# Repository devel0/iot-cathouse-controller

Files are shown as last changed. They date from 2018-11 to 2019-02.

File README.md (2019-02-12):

# iot-cathouse-controller

- [features](#features)
- [requirements](#requirements)
  * [thirdy part libraries](#thirdy-part-libraries)
- [initial setup](#initial-setup)
  * [set wifi ssid and pwd](#set-wifi-ssid-and-pwd)
  * [parameter configurations](#parameter-configurations)
  * [set temperature sensor ids](#set-temperature-sensor-ids)
- [config](#config)
  * [cooldown and system off](#cooldown-and-system-off)
  * [manual mode](#manual-mode)
  * [webapi](#webapi)
- [export csv data](#export-csv-data)
- [debug](#debug)
- [security considerations](#security-considerations)

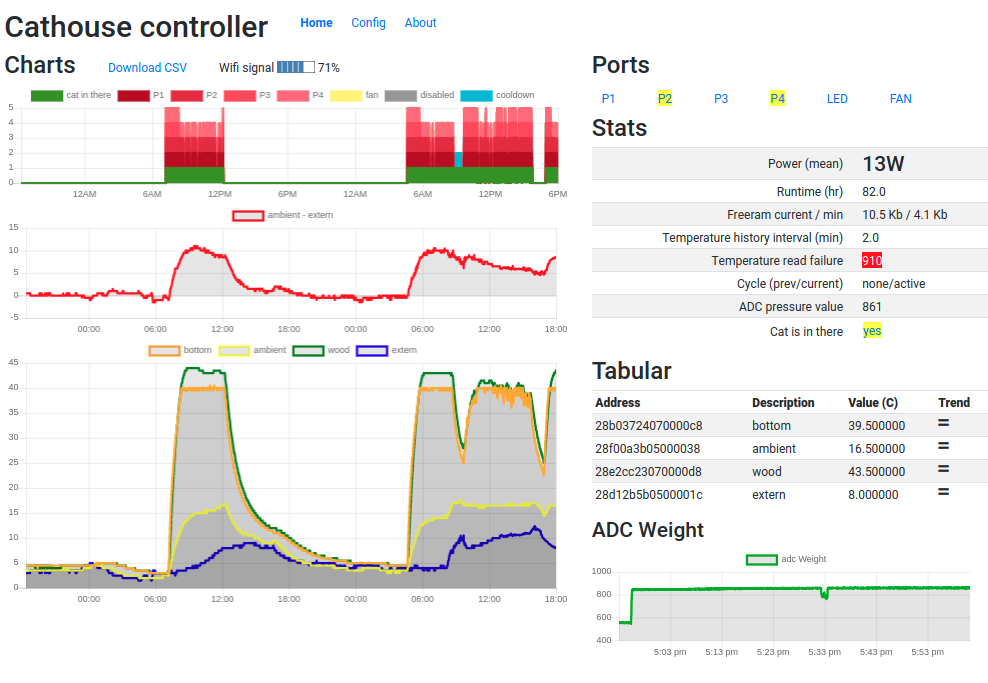
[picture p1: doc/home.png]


## features

- complete cathouse project ( building walls, heating system, weight detect, wifi control )
- wifi control automatic or manual through webapi ( [example](cathouse-analysis) )

## requirements

- hardware
  - [billing of materials](doc/bom.xlsx)
  - [instructables](https://www.instructables.com/id/DomoticCathouse/) to build and assembly cathouse parts
  - [nodemcu esp8266](https://www.google.com/search?q=nodemcu+esp8266)
  - [global schematics](https://easyeda.com/editor#id=|c888d1d962eb41688482b3634ec3ae96)
    - [mosfet driver](https://easyeda.com/editor#id=|8c9be83bc0324be699e9c5582d8d355a|41530c0b5fc0479b98395b739bd6d0e3)
    - [loadcell opamp](https://easyeda.com/editor#id=|20ec83ae7a4a4b50ac9ebe939533f176|184084caaad548a8a8d9fdd1c97d6a88|f6c7edf3d70e4a249dd6ca145c1bad17) and [sim](http://everycircuit.com/circuit/4874105232031744)
- software
  - [vscode arduino](https://github.com/devel0/knowledge/blob/master/electronics/vscode-arduino.md)
  - [esp8266 board plugin](https://github.com/esp8266/Arduino#installing-with-boards-manager)

### thirdy part libraries

- [ArduinoJsonWriter](https://github.com/maxpowel/ArduinoJsonWriter)
- [JsonStreamingParser](https://github.com/squix78/json-streaming-parser)
- [StringStream](https://gist.github.com/arcao/3252bb6e5e52493f03726ec32e61395c)

## initial setup

### set wifi ssid and pwd

connect to serial interface of esp8266 through usb cable with minicom at 115200 8N1 and issue `ctrl+c` to stop unsuccesful initial wifi connection then press `?` for SerialOS commands
- `set wifi ssid <ssid>` to set your own wifi ssid
- `set wifi pwd <pwd>` to set your own wifi pwd
- data save automatically into eeprom
- `reconnect` to test new wifi parameters
- check in the serial log which ip assigned to your device ( a better approach is to reserve a fixed wellknown ip address in your network by mapping it from the interface mac address also printed in serial log )

### parameter configurations

- connect to `http://cathouseip` and go to Config page

### set temperature sensor ids

in order to allow the system recognition of temperature sensor for bottom, wood, ambient and extern first there is the need to write down their ids ; use one of existing inet [articles](https://www.google.com/search?q=arduino+ds18b20+id) to find out.
write correspondent temperature IDs in fields ( 16 hex char foreach device )

### config

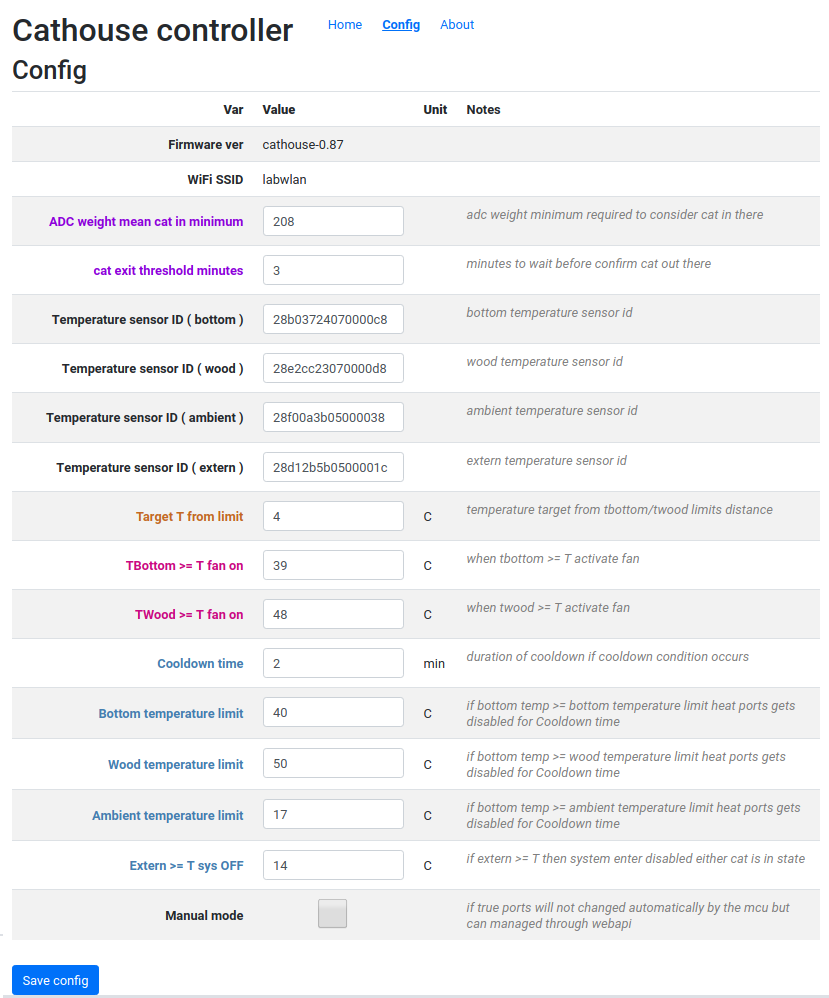
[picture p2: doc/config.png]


## heat modes

### auto mode

- when cat enters all ports enabled until reaches **Target T from limit** value from either one of bottom toward **Bottom temperature limit** or wood toward **Wood temperature limit**
- if some limit condition occurs system goes off for given cooldown time
  - bottom temp great or equals bottom temp limit
  - wood temp great or equals wood temp limit
  - ambient temp great or equals ambient temp limit
- if external temp great or equals 'Extern >= T sys OFF' then system goes off independently cat is in there or not
- ports are selected in order of preference as from [Config.h](cathouse-controller/Config.h) PORT_PREF
- trend delta can be configured in [Config.h](cathouse-controller/Config.h) TBOTTOM_TREND_DELTA_C

### manual mode

- in manual mode ports and fan can be controlled manually from web interface or webapi
- limit conditions still apply automatically entering the system in cooldown or disabled cycle mode
- led port can be toggled manually either in auto mode

### webapi

| **address** | **content-type** | **result example** |
|---|---|---|
| `/tempdevices` | json | `{"tempdevices":["28b03724070000c8","28f00a3b05000038","28e2cc23070000d8","28d12b5b0500001c"]}` |
| `/temp/devid` | text | retrieve temperature C of given `devid` device |
| `/info` | json | `{"wifiSignalStrength":-59, "statIntervalSec":2, "freeram":11464, "freeram_min":4168, "history_size":1455, "history_interval_sec":118, "temperatureHistoryFillCnt":1455, "temperatureHistoryOff":806, "temp_read_failure":915, "manualMode":false, "adcWeightArraySize":2048, "adcWeightArrayOff":273, "adcWeightArrayFillCnt":2048, "adcWeightArray":[848,847,849,848,...,850], "catIsInThere":true, "p1": false, "p2": true, "p3": false, "p4": true, "led": false, "fan": false, "temp_history_interval_min": 1.966667, "prev_cycle": "none", "current_cycle": "active", "runtime_hr": 82.190266, "Wh": 1087.330255}` |
| `/temphistory` | json | `[{"28b03724070000c8":[8.00,9.00]},{"28f00a3b05000038":[4.44,4]}]` |
| `/bithistories` | json | `{"catInThereHistory":[0,1,1],"p1History":[0,1,1],"p2History":[0,0,0],"p3History":[0,0,0],"p4History":[0,1,1],"fanHistory":[0,0,0],"disabledHistory":[0,0,0],"cooldownHistory":[0,0,0]}` |
| `/port/get/X` | text | `0` |
| `/port/set/X/{0,1}` | text | `OK` or `DENIED` if manualMode false |
| `/port/toggle/X` | text | `OK` or `DENIED` if manualMode false |
| `/setcatinthere/{0,1}` | text | `OK` |
| `/getconfig` | json | `{"tbottomLimit":45.00,"twoodLimit":60.00,"tambientLimit":17.00,"cooldownTimeMs":120000,"texternGTESysOff":14.00,"adcWeightMeanCatInMinimum":600,"catExitThresholdMin":3,"manualMode":false,"tbottomGTEFanOn":42.00,"twoodGTEFanOn":57.00,"targetTempFromLimit":4.00,"firmwareVersion":"cathouse-0.87","wifiSSID":"labwlan","tbottomId":"28b03724070000c8","twoodId":"28e2cc23070000d8","tambientId":"28f00a3b05000038","texternId":"28d12b5b0500001c"}` |
| `/saveconfig` | json POST | |

notes
- `temphistory`, `adcWeightArray`, `bithistories` are a set of measure where latest sample if the current one and previous are distant between each one from specified `history_interval_sec`
- valid ports in `/port/get` and `/port/set` are
  - heating ports ( 1, 2, 3, 4 )
  - led port ( 5 )
  - fan port ( 6 )

## export csv data

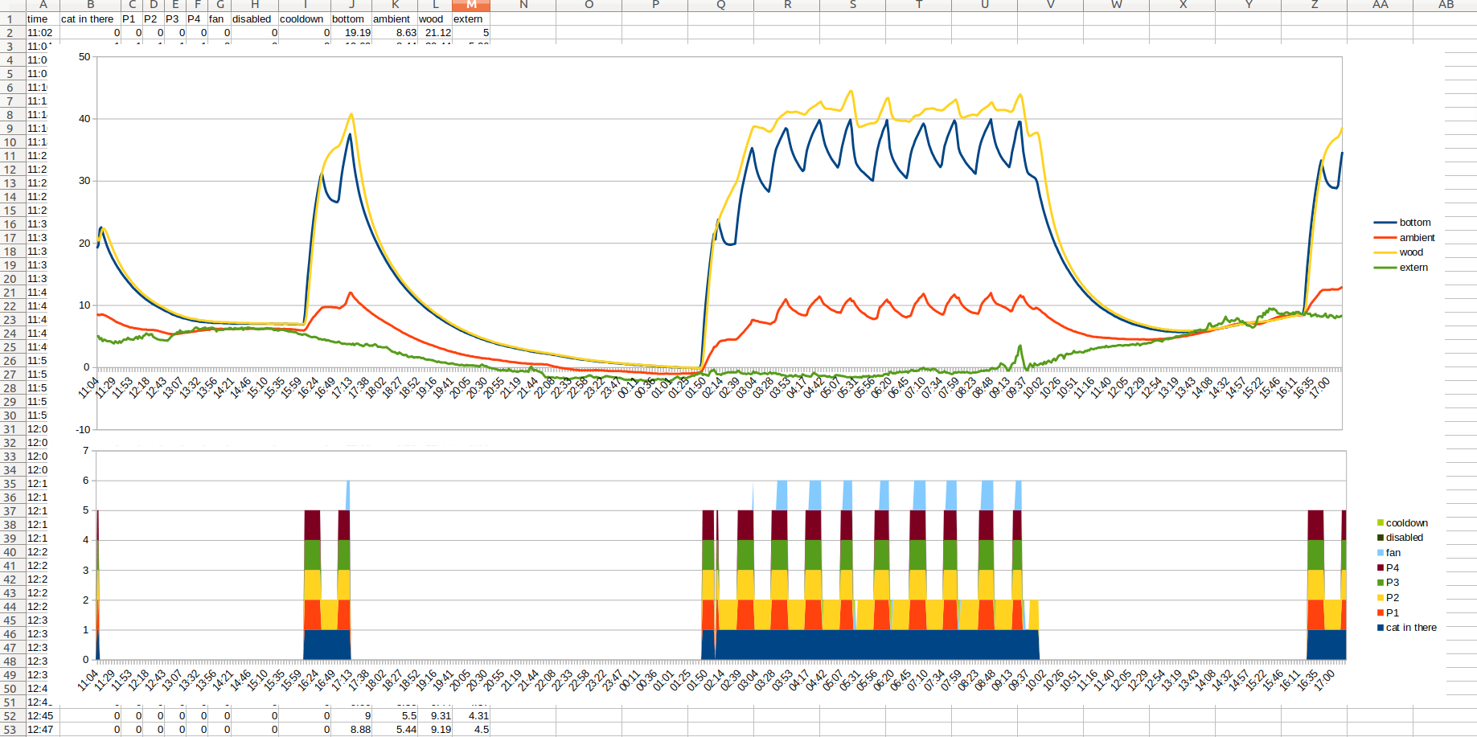
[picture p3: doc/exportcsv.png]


- data will be exported using decimal separator dot or comma accordingly to browser locale

## debug

```
cd cathouse-controller
code .
```

- to build or check compilation `CTRL+SHIFT+R`
- to upload through USB-serial `CTRL+SHIFT+U`

- when ENABLE_CORS enabled client side can be debugged without need to upload firmware again simply dragging `index.htm` to the browser so that `app.js` will loaded from local disk

## security considerations

- in release mode set [**ENABLE_CORS**](https://github.com/devel0/iot-cathouse-controller/blob/dbb4c67158c6660667ba5c55b46a064916e80611/cathouse-controller/Config.h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) to 0 to avoid browser requests from non owner html page
- on a internet facing page there is the need of a nginx proxy using a letsencrypt **https** certificate to ensure traffic flows in an encrypted channel ; plus there is the need to enable a page **basic authentication** ; see [here](https://github.com/devel0/knowledge/blob/cc771417542ff2cd5af335eec530da644a98c15a/webdevel/nginx-webapi-conf.md) for details

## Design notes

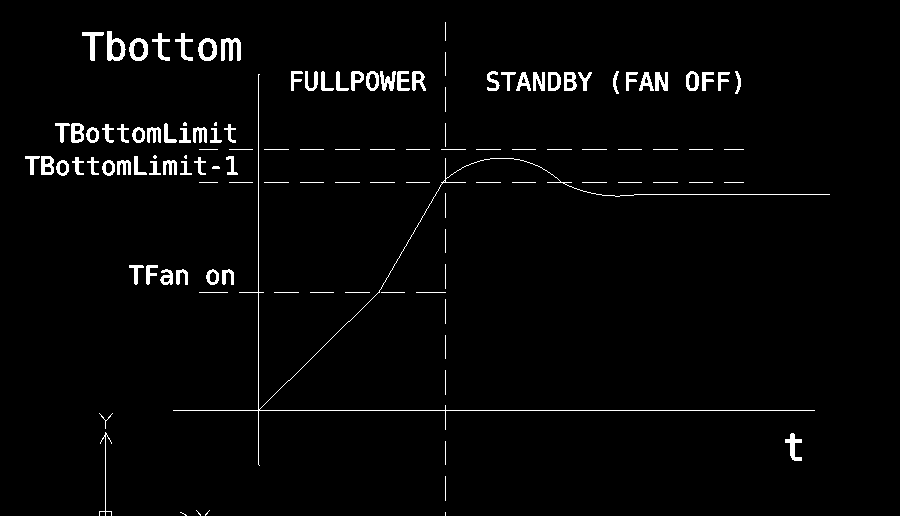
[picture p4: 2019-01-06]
doc/cycles.png

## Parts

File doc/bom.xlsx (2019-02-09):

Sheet: MATERIALS
qt | mu | description | L1 (mm) | L2 (mm) | thk (mm) | notes
2 |  | glass | 500 | 125 | 3
7 |  | polystyrene | 1000 | 500 | 10 | 4 x 830 x 600 + 2 x 556 x 600
13 |  | poplar plywood | 830 | 600 | 5 | 8 x 830 x 600 + 4 x 556 x 600 + 1 x 790 x 560
1 |  | poplar plywood | 830 | 400 | 5 | 1 x 700 x 400
4 |  | fir strip | 1000 | 97 | 10 | 2 x 780 + 2 x 550
1 |  | tierod M4 | 1000
2 |  | alu profile square hollow | 10 | 10 | 1000
2 |  | adhesive cold sealant | 25 | 5 | 4500
64 |  | screw | 15
12 |  | screw | 50
76 |  | washer | 10
2 | kg | refractory mortar

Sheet: 3DPRINT
part | qt | notes | license
spacer1.stl | 20 | top,bottom,front,back | MIT
spacer2.stl | 12 | left/right sides | MIT
spacer3.stl | 2 | door tierod holder | MIT
spacer4.stl | 2 | door fixating with tierod holder | MIT
cable-management.stl | 4 | ambient temp sensor and led wire holder | MIT
mosfet-driver-box | 1 |  | MIT
esp8266 holder | 1 | https://www.thingiverse.com/thing:3010027 | MIT
load-cell-5kg-contact-pad | 1 |  | MIT
load-cell-5kg-holder | 1 |  | MIT

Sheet: ELECTRONICS
category | qt | mu | description | code
fan | 1 |  | FAN 80mm 20mA @5V | Noctua NF-R8 Redux 1200
fan | 1 |  | resistor 3.3k ohm (5%)
heating | 1 |  | power transformer 24V 150W | MeanWell LRS-150-24
heating | 2 | m | Kanthal A1 AWG34 wire
heating | 4 |  | IRF740PBF mosfet
heating | 4 |  | TO-220 heatsink
heating | 4 |  | EL817 optocoupler
heating | 4 |  | PCB connector 1x2
heating | 4 |  | resistor 330 ohm (5%)
heating | 4 |  | resistor 10k ohm (5%)
led | 1 |  | white led flat 5mm 20mA
led | 1 |  | 2N2222 (1A max)
led | 1 |  | resistor 470 ohm (5%)
led | 1 |  | resistor 180 ohm (5%)
MCU | 1 |  | esp8266 nodemcu v3
power | 1 |  | power adaptor 5V 2A
temp sensor | 4 |  | ds18B20
temp sensor | 1 |  | resistor 4.7k ohm (1%)
weight sensor | 4 |  | loadcell 50kg SEN 10245
weight sensor | 1 |  | LM324N
weight sensor | 1 |  | PCB connector 1x2
weight sensor | 6 |  | resistor 39k (1%)
weight sensor | 1 |  | resistor 390 (5%)

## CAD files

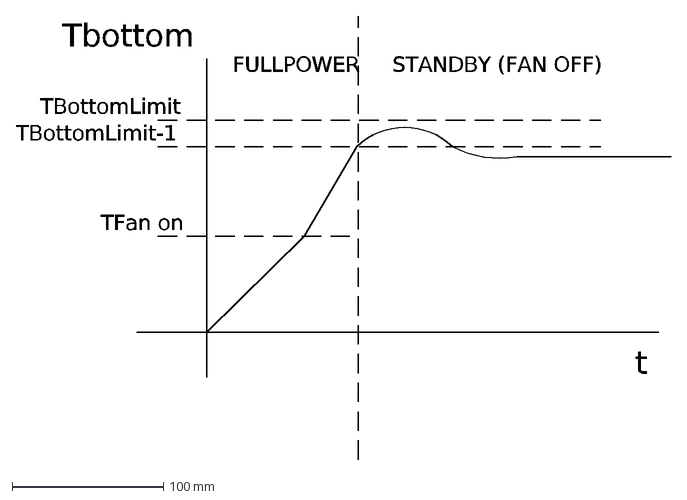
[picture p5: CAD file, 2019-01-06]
doc/auto-cycle.dxf
Tbottom
t
TFan on
TBottomLimit-1
TBottomLimit
FULLPOWER
STANDBY (FAN OFF)

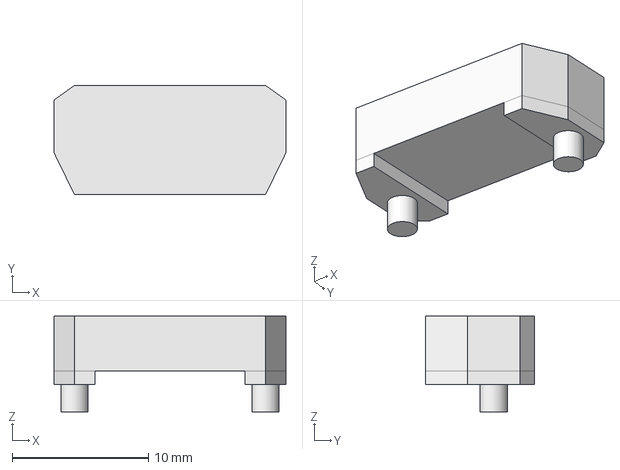
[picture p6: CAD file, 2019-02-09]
doc/cathouse-drawings/load-cell-5kg-contact-pad.fcstd
17.0 x 8.00 x 7.00 mm

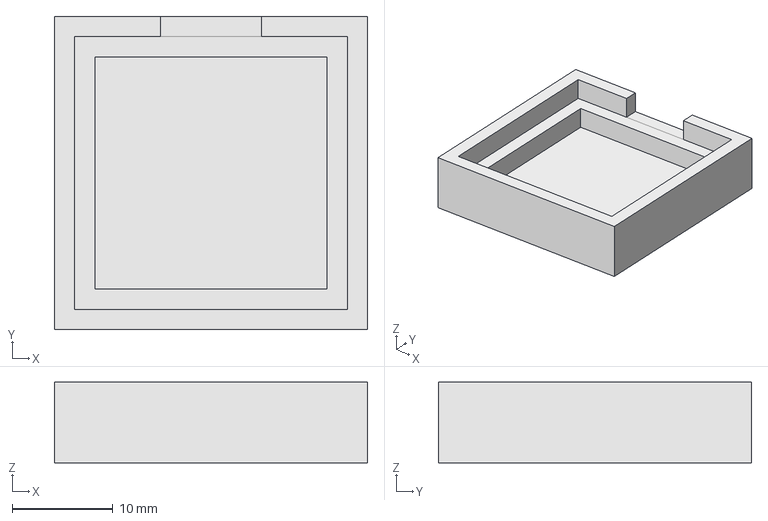
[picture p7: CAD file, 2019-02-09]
doc/cathouse-drawings/load-cell-5kg-holder.fcstd
31.0 x 31.0 x 8.00 mm

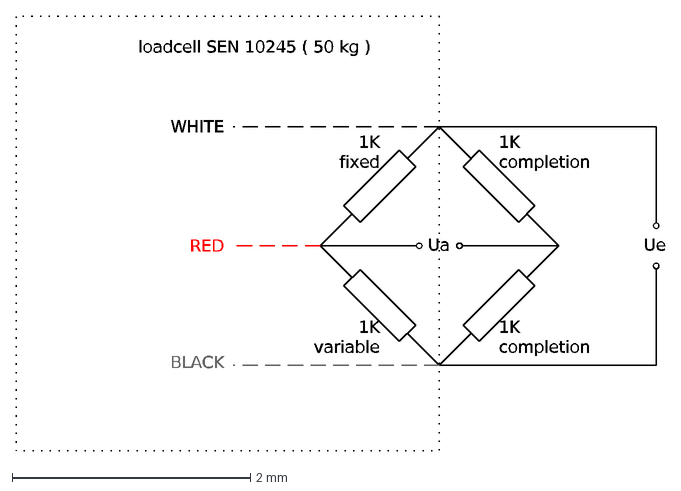
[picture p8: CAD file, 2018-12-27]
doc/loadcell-half-bridge-completion.dxf
1K completion
1K fixed
1K variable
Ua
Ue
RED
WHITE
BLACK
loadcell SEN 10245 ( 50 kg )

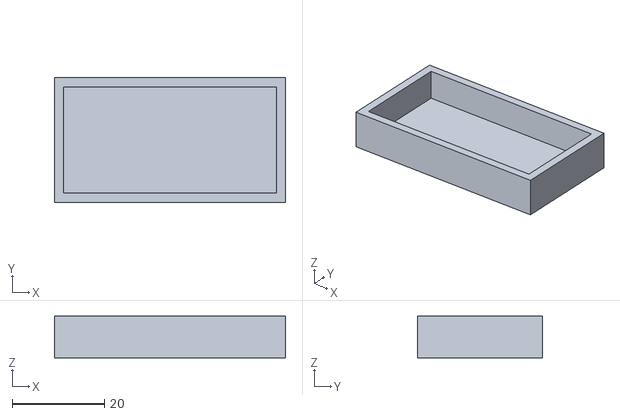
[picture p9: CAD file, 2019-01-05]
doc/cathouse-drawings/step-up-box.stl
50.0 x 27.0 x 9.00

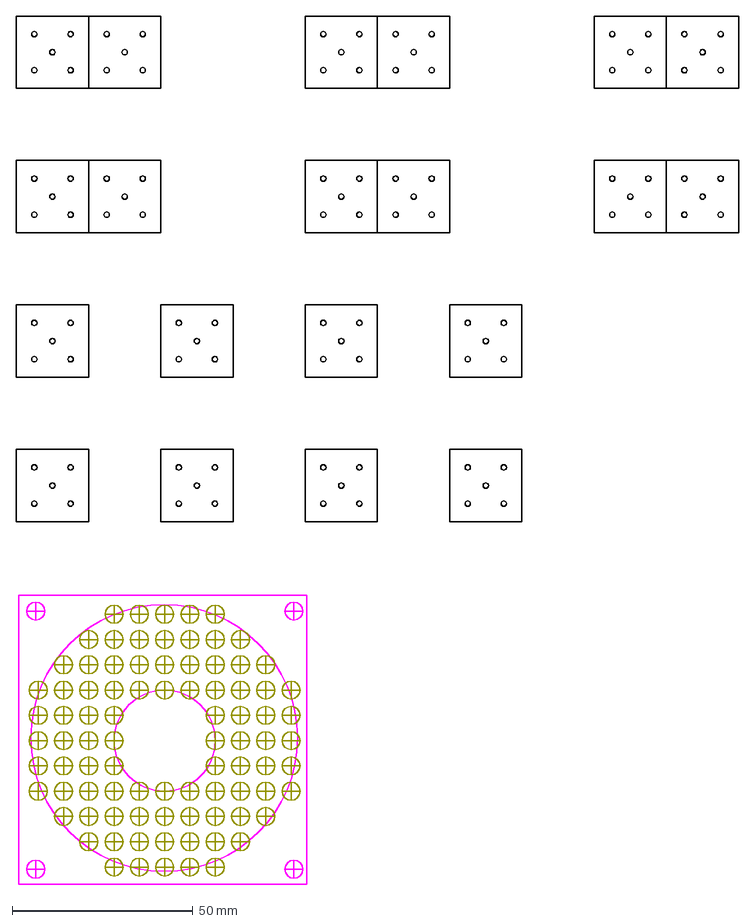
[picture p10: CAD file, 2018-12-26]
doc/cathouse-drawings/guidemask.dxf
200.0 x 240.3 mm

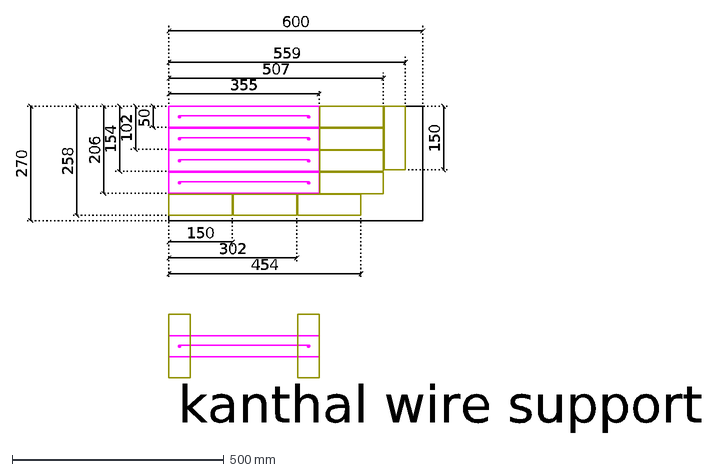
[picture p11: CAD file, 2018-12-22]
doc/cathouse-drawings/kanthal-wire-support.dxf
600
270
355
507
559
50
102
154
206
258
150
302
454
kanthal wire support

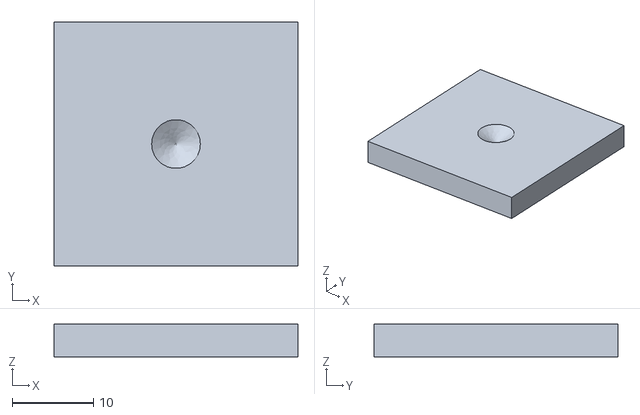
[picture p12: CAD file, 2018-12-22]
doc/cathouse-drawings/load-cell-top.stl
30.0 x 30.0 x 4.00

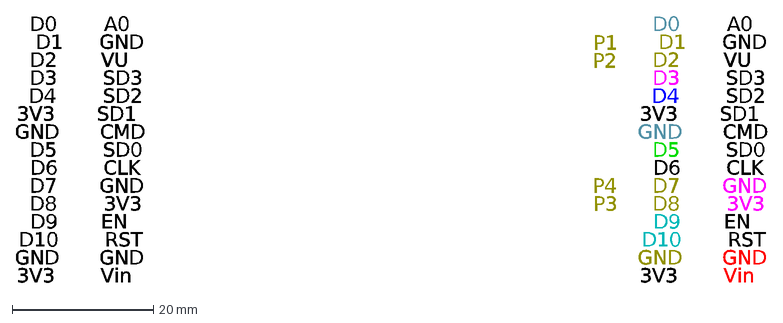
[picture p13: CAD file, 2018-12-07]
doc/cathouse-drawings/esp8266-labels.dxf
Vin
GND
RST
EN
3V3
CLK
SD0
CMD
SD1
SD2
SD3
VU
A0
D10
D9
D8
D7
D6
D5
D4
D3
D2
D1
D0
P1
P2
P4
P3

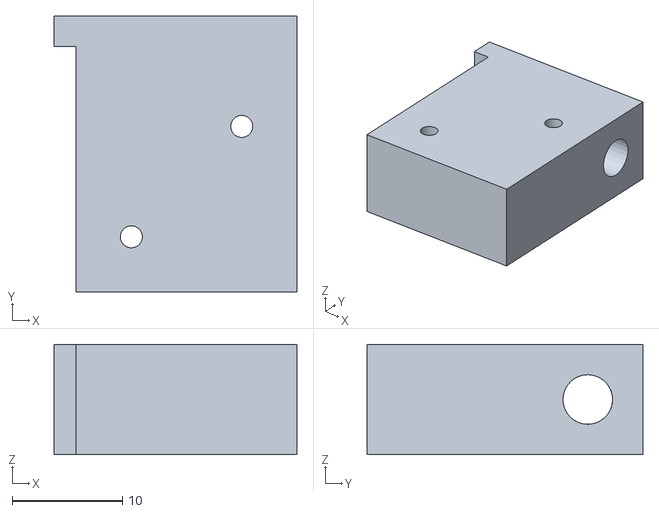
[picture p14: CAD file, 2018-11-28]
doc/cathouse-drawings/spacer4.stl
22.0 x 25.0 x 10.0

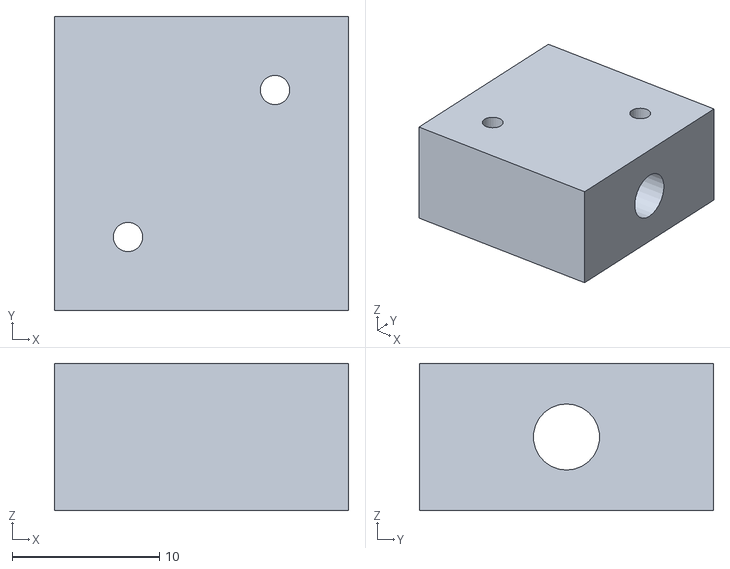
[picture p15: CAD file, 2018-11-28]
doc/cathouse-drawings/spacer3.stl
20.0 x 20.0 x 10.0

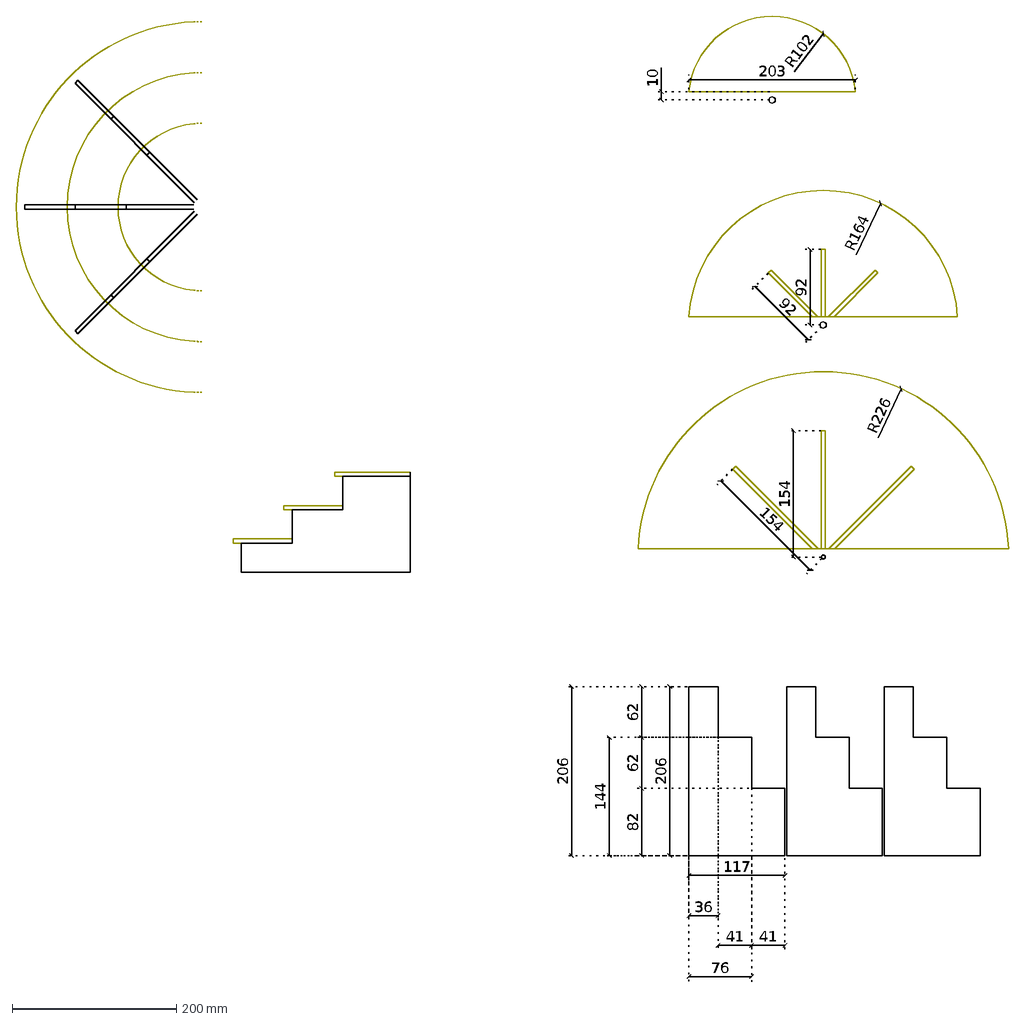
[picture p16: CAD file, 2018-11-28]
doc/cathouse-drawings/stairway.dxf
206
117
62
36
41
203
10
82
144
76
R164
R102
R226
154
92

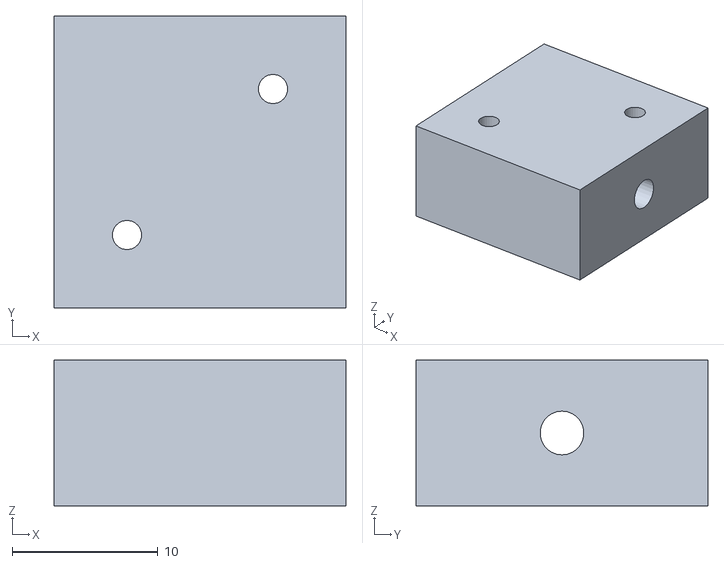
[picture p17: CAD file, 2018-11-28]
doc/cathouse-drawings/spacer2.stl
20.0 x 20.0 x 10.0

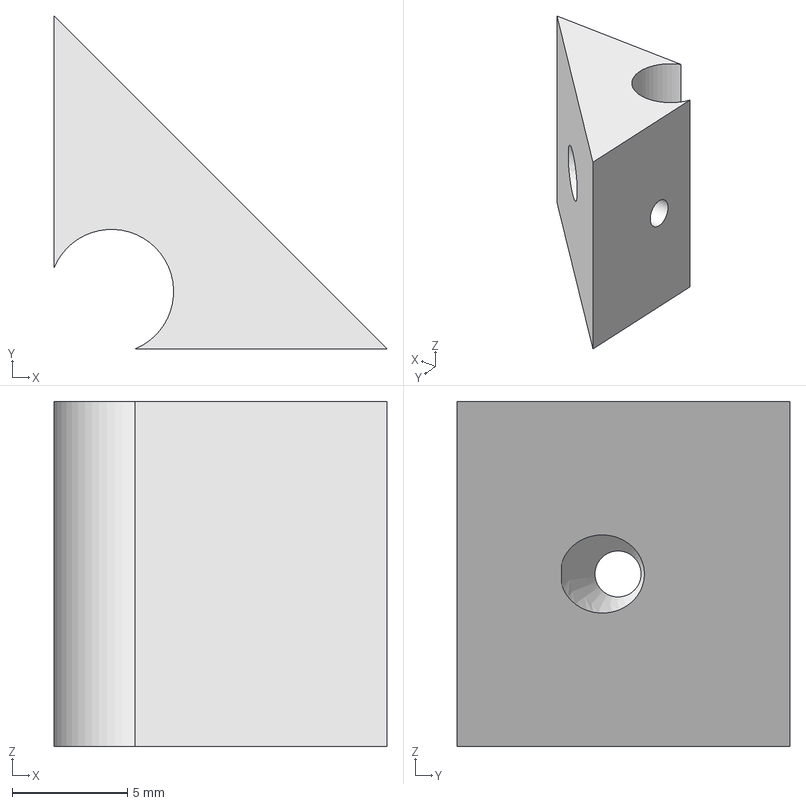
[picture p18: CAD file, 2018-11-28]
doc/cathouse-drawings/cable-management.fcstd
14.5 x 14.5 x 15.0 mm

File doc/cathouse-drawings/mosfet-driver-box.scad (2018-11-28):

//*************************************************
// VARIABLES
//*************************************************

// part to generate ( 0: box ; 1: top ; 2: all )
part = 0; // [0:box,1:top,2:all]

// wall thickness
wt = 2;

// lower support (x,y,z) thickness
lss = [ 5, 5, 4 ];

// internal object x,y,z size ( must consider required margins )
is = [ 104, 74, 10 ];

// object count
oc = 1;

// top interlock margin
tim = .5;

// top grid airflow ( >0 to enable or 0 to disable )
tg = 0;

// top grid airflow wall thickness
tgwt = 5;

// hole (width, height, xcenter, xcenter_percent, zbottom)
// notes: if xcenter_percent true when pos represent position 0..1 inside
// zbottom is the distance from bottom to the begin of hole

// left holes ( array of [width, height, xcenter, xcenter_percent, zbottom] )
lh = [];

// right holes ( array of [width, height, xcenter, xcenter_percent, zbottom] )
rh = [];

// front holes ( array of [width, height, xcenter, xcenter_percent, zbottom] )
fh = [ ];

// bottom holes ( array of [width, height, xcenter, xcenter_percent, zbottom] )
bh = [];
//bh = fh;

//*************************************************
//
//*************************************************

// total size
ts = [
    wt + oc * ( is[0] + wt ),
    is[1] + 2 * wt,
    wt + lss[2] + is[2] + 2 * wt
];

someholes = (len(lh) + len(rh) + len(fh) + len(bh)) > 0;

//======================================
// part: 0 ( BOX and HOLES )
//======================================
module box()
{
    wt3 = [wt, wt, wt];
    
    // box size
    bs = [ ts[0], ts[1], ts[2] - wt ];
    
    color("DarkGray", alpha=.5)
    {
        union()
        {    

            // main box
            difference()
            {
                cube(bs);
                translate(wt3)
                    cube([ts[0] - 2 * wt, bs[1] - 2 * wt, bs[2]]);
            }
            
            // pcb support
            translate(wt3)
            {
                difference()
                {
                    cube([
                        bs[0] - 2 * wt,
                        bs[1] - 2 * wt,
                        lss[2]
                    ]);
                    translate([lss[0], lss[1], 0])
                        cube([
                            bs[0] - 2 * wt - 2 * lss[0],
                            bs[1] - 2 * wt - 2 * lss[1],
                            lss[2]
                        ]);
                }
            }
            
            // objs sep walls with lower support
            if (oc > 1)
            {
                for (i = [1:oc-1])
                {
                    // wall
                    translate([i * (wt + is[0]), 0, 0])
                        cube([wt, bs[1], wt + lss[2] + is[2]]);
                    
                    // near support
                    translate([i * (wt + is[0]) - lss[0], 0, wt])        
                        cube([lss[0], bs[1], lss[2]]);
                    
                    // far support
                    translate([i * (wt + is[0]) + wt, 0, wt])        
                        cube([lss[0], bs[1], lss[2]]);
                }
            }
        }
    }
}

module holes()
{
    // front holes
    if (len(fh) > 0)
    {
        for (i = [0 : len(fh)-1])
        {    
            hole = fh[i];        
            
            w = hole[0];
            h = hole[1];        
            
            xpos = wt + i * (is[0] + wt) + 
                (hole[3] ? is[0] * hole[2] : hole[2]) - w/2;
            zpos = hole[4];
                    
            translate([xpos, 0, zpos])
                cube([w, wt + lss[1], h]);                
        }
    }
    
    // back holes
    if (len(bh) > 0)
    {
        for (i = [0 : len(bh)-1])
        {    
            hole = bh[i];        
            
            w = hole[0];
            h = hole[1];        
            
            xpos = wt + i * (is[0] + wt) + 
                (hole[3] ? is[0] * hole[2] : hole[2]) - w/2;
            zpos = hole[4];
                    
            translate([xpos, ts[1] - wt - lss[1], zpos])
                cube([w, wt + lss[1], h]);                
        }
    }
    
    // left holes
    if (len(lh) > 0)
    {
        for (i = [0 : len(lh)-1])
        {    
            hole = lh[i];                
            
            w = hole[0];
            h = hole[1];        
            
            ypos = wt + 
                (hole[3] ? is[1] * hole[2] : hole[2]) - w/2;
            zpos = hole[4];
                    
            translate([0, ypos, zpos])
                cube([wt + lss[1], w, h]);                
        }
    }
    
    // right holes
    if (len(rh) > 0)
    {
        for (i = [0 : len(rh)-1])
        {    
            hole = rh[i];                
            
            w = hole[0];
            h = hole[1];        
            
            ypos = wt + 
                (hole[3] ? is[1] * hole[2] : hole[2]) - w/2;
            zpos = hole[4];
                    
            translate([ts[0] - wt - lss[1], ypos, zpos])
                cube([wt + lss[1], w, h]);                
        }
    }
}

if (part == 0 || part == 2)
{
    difference()
    {
        box();
        if (someholes) holes();
    }
}

//======================================
// part: 1 ( TOP )
//======================================
module topGrid()
{
    if (tg > 0)
    {                
        // avx,y space after required margin
        avx = ts[0] - 4 * wt;
        avy = ts[1] - 4 * wt;
        
        dimx = tg + tgwt;
        dimy = tg + tgwt;
                                
        kx = floor(avx / dimx);
        offx = (ts[0] - kx * dimx) / 2 + tgwt / 2;
                
        ky = floor(avy / dimy);
        offy = (ts[1] - ky * dimy) / 2 + tgwt / 2;
        
        echo(ts[0]/oc);
        
        for (ix = [0:kx-1])
        {
            for (iy = [0:ky-1])
            {                                                
                tx = offx + ix * dimx;
                ty = offy + iy * dimy;
                
                if ((tx + dimx/2) % (ts[0]/oc) > wt + dimx/2)
                {                
                    translate([tx, ty, ts[2] - 2 * wt])
                        cube([tg, tg, 2 * wt]);
                }
            }
        }
    }
}

module top_()
{
    color("Coral", alpha=.5)    
    {
        // top
        translate([0, 0, ts[2]-wt])
            cube([ts[0], ts[1], wt]);
        
        // top interlock
        translate([wt + tim, wt + tim, ts[2] - 2 * wt])
            cube([ts[0] - 2 * wt - 2 * tim, ts[1] - 2 * wt - 2 * tim, wt]);
    }
}

module top()
{
    difference()
    {
        top_();
        topGrid();
    }    
}
if (part == 1 || part == 2)
{
    top();
}

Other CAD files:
doc/cathouse-drawings/loadcell-50kg-mask.fcstd
doc/cathouse-drawings/project.dxf
doc/cathouse-drawings/wood-cuts.dxf
doc/cathouse-drawings/spacer1.fcstd
doc/cathouse-drawings/cable-management.dxf
doc/cathouse-drawings/cable-management.stl
doc/cathouse-drawings/load-cell-5kg-contact-pad.dxf
doc/cathouse-drawings/load-cell-5kg-contact-pad.stl
doc/cathouse-drawings/load-cell-5kg-holder.dxf
doc/cathouse-drawings/load-cell-5kg-holder.stl
doc/cathouse-drawings/mosfet-driver-box.stl
doc/cathouse-drawings/old/loadcell-50kg-mask.fcstd
doc/cathouse-drawings/spacer1.stl

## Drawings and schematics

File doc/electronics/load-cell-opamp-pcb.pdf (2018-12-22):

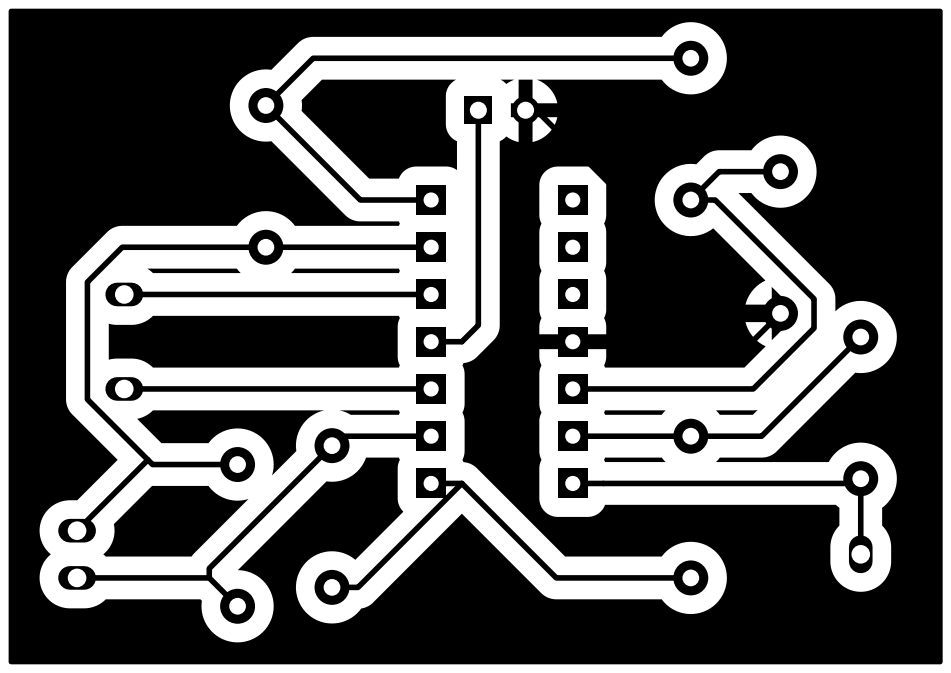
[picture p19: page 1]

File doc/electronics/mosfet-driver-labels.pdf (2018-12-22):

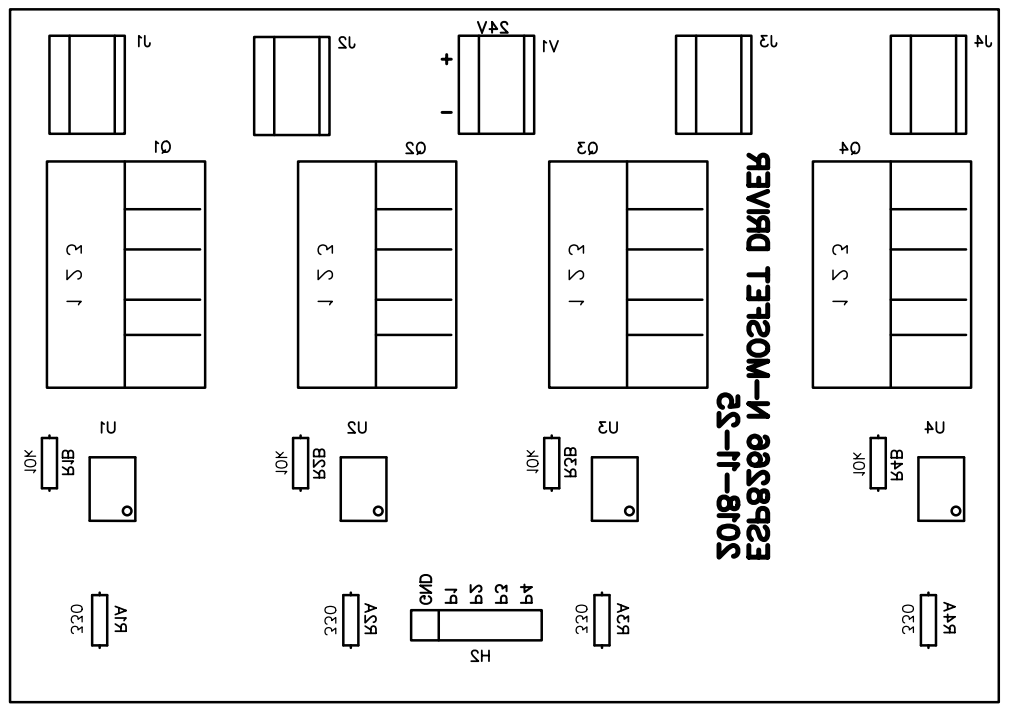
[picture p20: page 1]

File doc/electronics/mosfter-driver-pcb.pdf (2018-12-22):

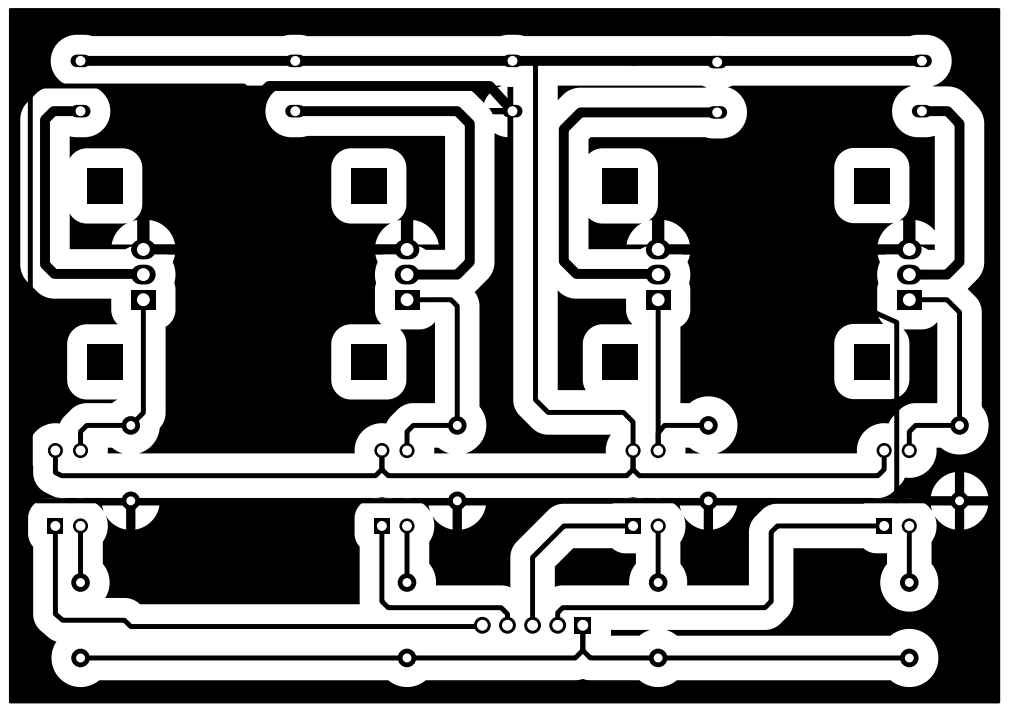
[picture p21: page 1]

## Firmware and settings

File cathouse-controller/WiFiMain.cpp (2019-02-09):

#include "WiFiMain.h"
#include "WiFiUtil.h"
#include "Config.h"
#include "Util.h"
#include "EEJsonConfig.h"
#include "SList.h"
#include "TempDev.h"
#include "Stats.h"
#include "WeightDev.h"
#include "Engine.h"

#include <ArduinoJson.h>

WiFiServer server(WEB_PORT);

String header;

//
// WiFi main cycle
//
bool manageWifi()
{
  WiFiClient client = server.available();

  if (client)
  {
    String currentLine = "";

    while (client.connected())
    {
      if (client.available())
      {
        char c = client.read();
        if (c != '\n')
          header += c;
        else
        {
          int newlinecnt = 0;
          while (client.available() || newlinecnt != 2) // discard rest of header
          {
            c = client.read();

            if (c == '\n')
            {
              if (newlinecnt == 1)
                break;
              else
                newlinecnt = 1;
            }
            else if (c != '\r')
              newlinecnt = 0;
          }

          //-----------------------------------------------
          // /
          //-----------------------------------------------
          if (header.indexOf("GET / ") >= 0 || header.indexOf("GET /index.htm") >= 0)
          {
            clientOk(client, HTML);

            clientWriteBigString(client,
#include "index.htm.h"
            );
          }
          //-----------------------------------------------
          // /app.js
          //-----------------------------------------------
          else if (header.indexOf("GET /app.js ") >= 0)
          {
            clientOk(client, JAVASCRIPT);

            clientWriteBigString(client,
#include "app.js.h"
            );
          }
          //--------------------------
          // /tempdevices
          //--------------------------
          else if (header.indexOf("GET /tempdevices ") >= 0)
          {
            clientOk(client, JSON);

            client.print(F("{\"tempdevices\":["));
            for (int i = 0; i < temperatureDeviceCount; ++i)
            {
              client.print('"');
              client.print(tempDevHexAddress[i]);
              client.print('"');

              if (i != temperatureDeviceCount - 1)
                client.print(',');
            }
            client.print("]}");
          }
          //--------------------------
          // /temp/{id}
          //--------------------------
          else if (header.indexOf("GET /temp/") >= 0)
          {
            auto tid = header.substring(10);
            tid = tid.substring(0, tid.indexOf(" "));
            //Serial.printf("query for device id = %s]\n", tid.c_str());
            bool found = false;

            clientOk(client, TEXT);

            for (int i = 0; i < temperatureDeviceCount; ++i)
            {
              if (tid.equals(tempDevHexAddress[i]))
              {
                char tmp[20];
                snprintf(tmp, 19, "%f", temperatures[i]);

                client.print(tmp);

                found = true;
                break;
              }
            }

            if (!found)
              client.print(F("not found"));
          }
          //--------------------------
          // /temphistory
          //--------------------------
          else if (header.indexOf("GET /temphistory ") >= 0)
          {
            clientOk(client, JSON);

            //Serial.printf("temperatureHistoryFillCnt: %d Off:%d\n", temperatureHistoryFillCnt, temperatureHistoryOff);

            client.print('[');
            for (int i = 0; i < temperatureDeviceCount; ++i)
            {
              client.print(F("{\""));
              client.print(tempDevHexAddress[i]);
              client.print(F("\":["));
              auto j = (temperatureHistoryFillCnt == temperatureHistorySize) ? temperatureHistoryOff : 0;
              auto size = min(temperatureHistoryFillCnt, temperatureHistorySize);
              for (int k = 0; k < size; ++k)
              {
                if (j == temperatureHistorySize)
                  j = 0;
                client.print(temperatureHistory[i][j++]);
                if (k < size - 1)
                  client.print(',');
              }
              client.print(F("]}"));
              if (i != temperatureDeviceCount - 1)
                client.print(',');
            }
            client.print(']');
          }
          //--------------------------
          // /bithistories
          //--------------------------
          else if (header.indexOf("GET /bithistories ") >= 0)
          {
            clientOk(client, JSON);

            client.print('{');
            auto startoff = (temperatureHistoryFillCnt == temperatureHistorySize) ? temperatureHistoryOff : 0;
            auto size = min(temperatureHistoryFillCnt, temperatureHistorySize);

            {
              client.print("\"catInThereHistory\":[");
              auto j = startoff;
              for (int k = 0; k < size; k++)
              {
                if (j == temperatureHistorySize)
                  j = 0;
                client.print(catInThereHistory->Get(j++) ? "1" : "0");

                if (k < size - 1)
                  client.print(',');
              }
              client.print("]");
            }

            {
              client.print(",\"p1History\":[");
              auto j = startoff;
              for (int k = 0; k < size; k++)
              {
                if (j == temperatureHistorySize)
                  j = 0;
                client.print(p1History->Get(j++) ? "1" : "0");

                if (k < size - 1)
                  client.print(',');
              }
              client.print("]");
            }

            {
              client.print(",\"p2History\":[");
              auto j = startoff;
              for (int k = 0; k < size; k++)
              {
                if (j == temperatureHistorySize)
                  j = 0;
                client.print(p2History->Get(j++) ? "1" : "0");

                if (k < size - 1)
                  client.print(',');
              }
              client.print("]");
            }

            {
              client.print(",\"p3History\":[");
              auto j = startoff;
              for (int k = 0; k < size; k++)
              {
                if (j == temperatureHistorySize)
                  j = 0;
                client.print(p3History->Get(j++) ? "1" : "0");

                if (k < size - 1)
                  client.print(',');
              }
              client.print("]");
            }

            {
              client.print(",\"p4History\":[");
              auto j = startoff;
              for (int k = 0; k < size; k++)
              {
                if (j == temperatureHistorySize)
                  j = 0;
                client.print(p4History->Get(j++) ? "1" : "0");

                if (k < size - 1)
                  client.print(',');
              }
              client.print("]");
            }

            {
              client.print(",\"fanHistory\":[");
              auto j = startoff;
              for (int k = 0; k < size; k++)
              {
                if (j == temperatureHistorySize)
                  j = 0;
                client.print(fanHistory->Get(j++) ? "1" : "0");

                if (k < size - 1)
                  client.print(',');
              }
              client.print("]");
            }

            {
              client.print(",\"disabledHistory\":[");
              auto j = startoff;
              for (int k = 0; k < size; k++)
              {
                if (j == temperatureHistorySize)
                  j = 0;
                client.print(disabledHistory->Get(j++) ? "1" : "0");

                if (k < size - 1)
                  client.print(',');
              }
              client.print("]");
            }

            {
              client.print(",\"cooldownHistory\":[");
              auto j = startoff;
              for (int k = 0; k < size; k++)
              {
                if (j == temperatureHistorySize)
                  j = 0;
                client.print(cooldownHistory->Get(j++) ? "1" : "0");

                if (k < size - 1)
                  client.print(',');
              }
              client.print("]");
            }

            client.print('}');
          }
          //--------------------------
          // /info
          //--------------------------
          else if (header.indexOf("GET /info ") >= 0)
          {
            clientOk(client, JSON);

            client.print('{');

            client.print(F("\"wifiSignalStrength\":"));
            client.print(WiFi.RSSI());

            client.print(F(", \"statIntervalSec\":"));
            client.print(UPDATE_STATS_INTERVAL_MS / 1000);

            client.print(F(", \"freeram\":"));
            client.print(freeram);

            client.print(F(", \"freeram_min\":"));
            client.print(freeram_min);

            client.print(F(", \"history_size\":"));
            client.print(temperatureHistorySize);

            client.print(F(", \"history_interval_sec\":"));
            client.print(temperatureHistoryIntervalSec);

            client.print(F(", \"temperatureHistoryFillCnt\":"));
            client.print(temperatureHistoryFillCnt);

            client.print(F(", \"temperatureHistoryOff\":"));
            client.print(temperatureHistoryOff);

            client.print(F(", \"temp_read_failure\":"));
            client.print(tempReadFailure);

            client.print(F(", \"manualMode\":"));
            client.print(eeJsonConfig.manualMode ? "true" : "false");            

            client.print(F(", \"adcWeightArraySize\":"));
            client.print(adcWeightArraySize);

            client.print(F(", \"adcWeightArrayOff\":"));
            client.print(adcWeightArrayOff);

            client.print(F(", \"adcWeightArrayFillCnt\":"));
            client.print(adcWeightArrayFillCnt);

            client.print(F(", \"adcWeightArray\":["));
            {
              auto wstart = adcWeightArrayFillCnt == adcWeightArraySize ? adcWeightArrayOff : 0;
              for (int i = wstart; i < wstart + adcWeightArrayFillCnt; ++i)
              {
                client.printf("%d", adcWeightArray[i % adcWeightArraySize]);
                if (i < wstart + adcWeightArrayFillCnt - 1)
                  client.print(",");
              }
            }
            client.print(F("]"));

            client.print(F(", \"catIsInThere\":"));
            client.print(catInThere ? "true" : "false");

            for (int i = 0; i < 4; ++i)
            {
              client.printf(", \"p%d\": ", i + 1);
              auto port = portToPin(i + 1);
              if (digitalRead(port) == HIGH)
                client.print("true");
              else
                client.print("false");
            }

            if (digitalRead(LED_PIN) == HIGH)
              client.printf(", \"led\": true");
            else
              client.printf(", \"led\": false");

            if (digitalRead(FAN_PIN) == HIGH)
              client.printf(", \"fan\": true");
            else
              client.printf(", \"fan\": false");

            client.printf(", \"temp_history_interval_min\": %f", temperatureHistoryIntervalSec / 60.0);
            client.printf(", \"prev_cycle\": \"%s\"", getCycleStr(prevCycle).c_str());
            client.printf(", \"current_cycle\": \"%s\"", getCycleStr(currentCycle).c_str());

            client.printf(", \"runtime_hr\": %f", runtime_hr);
            client.printf(", \"Wh\": %f", Wh);

            client.print('}');
          }
          //--------------------------
          // /port/get/{1,2,3,4,5,6,7}
          // note: 5 is led, 6 is fan, 7 is weight (0-1023 adc)
          //--------------------------
          else if (header.indexOf("GET /port/get/") >= 0)
          {
            clientOk(client, TEXT);

            auto port = header.substring(14);
            port = port.substring(0, port.indexOf(" "));

            //Serial.printf("port = [%s]\n", port.c_str());

            if (port == "1")
              client.print(digitalRead(MOSFET_P1));

            else if (port == "2")
              client.print(digitalRead(MOSFET_P2));

            else if (port == "3")
              client.print(digitalRead(MOSFET_P3));

            else if (port == "4")
              client.print(digitalRead(MOSFET_P4));

            else if (port == "5")
              client.print(digitalRead(LED_PIN));

            else if (port == "6")
              client.print(digitalRead(FAN_PIN));

            else if (port == "7")
              client.print(analogRead(A0));
          }
          //--------------------------
          // /port/set/{1,2,3,4,5,6}/{0,1}
          // note: 5 is led, 6 is fan
          //--------------------------
          else if (header.indexOf("GET /port/set/") >= 0)
          {
            clientOk(client, TEXT);

            auto str = header.substring(14);
            auto port = str.substring(0, str.indexOf("/"));
            auto mode = str.substring(str.indexOf("/") + 1, str.indexOf(" "));

            //Serial.printf("setting port [%s] to [%s]\n", port.c_str(), mode.c_str());

            auto portnr = atoi(port.c_str());
            auto modenr = atoi(mode.c_str());

            int portpin = MOSFET_P1;

            switch (portnr)
            {
            case 1:
              portpin = MOSFET_P1;
              break;
            case 2:
              portpin = MOSFET_P2;
              break;
            case 3:
              portpin = MOSFET_P3;
              break;
            case 4:
              portpin = MOSFET_P4;
              break;
            case 5:
              portpin = LED_PIN;
              break;
            case 6:
              portpin = FAN_PIN;
              break;
            }

            if (!eeJsonConfig.manualMode && portpin != LED_PIN)
            {
              client.print("DENIED");
            }
            else
            {
              auto v = digitalRead(portpin);
              if (modenr)
                digitalWrite(portpin, HIGH);
              else
                digitalWrite(portpin, LOW);

              Serial.printf("manual> set port %d from %d\n", portnr, v);
              setManual();

              client.print("OK");
            }
          }
          //--------------------------
          // /port/toggle/{1,2,3,4,5,6}
          // note: 5 is led, 6 is fan
          //--------------------------
          else if (header.indexOf("GET /port/toggle/") >= 0)
          {
            clientOk(client, TEXT);

            auto str = header.substring(17);
            auto port = str.substring(0, str.indexOf(" "));

            auto portnr = atoi(port.c_str());

            int portpin = MOSFET_P1;

            switch (portnr)
            {
            case 1:
              portpin = MOSFET_P1;
              break;
            case 2:
              portpin = MOSFET_P2;
              break;
            case 3:
              portpin = MOSFET_P3;
              break;
            case 4:
              portpin = MOSFET_P4;
              break;
            case 5:
              portpin = LED_PIN;
              break;
            case 6:
              portpin = FAN_PIN;
              break;
            }

            if (!eeJsonConfig.manualMode && portpin != LED_PIN)
            {
              client.print("DENIED");
            }
            else
            {
              auto v = digitalRead(portpin);
              Serial.printf("manual> toggling port %d from %d\n", portnr, v);
              digitalWrite(portpin, (v == LOW) ? HIGH : LOW);
              setManual();

              client.print("OK");
            }
          }
          //--------------------------
          // /setcatinthere/{0,1}
          //--------------------------
          else if (header.indexOf("GET /setcatinthere/") >= 0)
          {
            clientOk(client, TEXT);

            auto arg = header.substring(19);
            auto str = arg.substring(0, arg.indexOf(" "));
            auto changed = false;

            if (str == "0")
            {
              changed = catInThere;
              catInThere = false;
              catInThereOverriden = false;
            }
            else
            {
              changed = !catInThere;
              catInThere = true;
              catInThereOverriden = true;
            }

            Serial.printf("engine> override catInThere = %d\n", catInThere ? 1 : 0);

            client.print("OK");
          }
          //-----------------------------------------------
          // /getconfig
          //-----------------------------------------------
          else if (header.indexOf("GET /getconfig ") >= 0)
          {
            //WiFiPrinter prn(client);

            clientOk(client, JSON);

            eeJsonConfig.Save(client, true);
          }
          //-----------------------------------------------
          // /saveconfig
          //-----------------------------------------------
          else if (header.indexOf("POST /saveconfig ") >= 0)
          {
            clientOk(client, TEXT);

            String s;
            while (client.available() || (client.peek() != -1)) // read all frames
            {
              while (client.available())
              {
                auto c = (char)client.read();
                s.concat(c);
              }
              client.flush();
            }
            Serial.printf("saving config [%s]\n", s.c_str());

            auto wasManual = eeJsonConfig.manualMode;

            eeJsonConfig.Load(s.c_str());
            eeJsonConfig.SaveToEEProm();
            if (eeStaticConfigDirty)
            {
              saveEEStaticConfig();
              eeStaticConfigDirty = false;
            }

            if (currentCycle == manual && !eeJsonConfig.manualMode)
              unsetManual();
          }

          header = "";
          break;
        }
      }
    }

    client.stop();

    return true;
  }

  client.stop();

  return false;
}

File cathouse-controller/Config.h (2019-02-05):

#ifndef _CONFIG_H_
#define _CONFIG_H_

#define FIRMWARE_VER "cathouse-0.87"

#include <Arduino.h>

#define SERIAL_SPEED 115200
#define WEB_PORT 80
#define ENABLE_CORS 1

#define ADCWEIGHT_PIN A0

#define ONEWIRE_PIN D3
#define LED_BUILTIN D4
#define LED_PIN D5
#define FAN_PIN D0

#define MOSFET_P1 D1
#define MOSFET_P2 D2
#define MOSFET_P3 D8
#define MOSFET_P4 D7

// measured system power / 4
#define W_PORT 26.75

// ease initial simulation of daily cat out there 8 hr
#define INITIAL_EMPTY_RUNTIME_HR 8

#define UPDATE_STATS_INTERVAL_MS 2000
#define UPDATE_TEMPERATURE_INTERVAL_MS 5000
#define FREERAM_THRESHOLD_MIN_BYTES (10*1024)
#define TEMPERATURE_HISTORY_BACKLOG_HOURS 48
#define ADCWEIGHT_HISTORY_BACKLOG_KB 4
#define ENGINE_POOL_INTERVAL_MS 5000
#define ENGINE_STANDBY_REACTION_INTERVAL_MS 60000
#define ENGINE_FAN_DEACTIVATION_THRESHOLD_MIN 1

// port preference order
#define PORT_PREF_1 MOSFET_P2
#define PORT_PREF_2 MOSFET_P4
#define PORT_PREF_3 MOSFET_P1
#define PORT_PREF_4 MOSFET_P3

#define TBOTTOM_TREND_DELTA_C 0.5

#define FACTORY_TBOTTOM_LIMIT 45
#define FACTORY_TWOOD_LIMIT 60
#define FACTORY_TAMBIENT_LIMIT 17
#define FACTORY_COOLDOWN_TIME_MS (2*60*1000)
#define FACTORY_TEXTERN_GTE_SYS_OFF 14
#define FACTORY_ADC_WEIGHT_MEAN_CATIN_MINIMUM 300
#define FACTORY_CATEXIT_THRESHOLD_MIN 3
#define FACTORY_TBOTTOM_GTE_FAN_ON 42
#define FACTORY_TWOOD_GTE_FAN_ON 57
#define FACTORY_TARGET_TEMP_FROM_LIMIT 4
#define FACTORY_MANUAL_MODE false
#define FACTORY_FANLESS_MODE true

// port {1,2,3,4,5,6} to pin
int portToPin(int pin);

#endif

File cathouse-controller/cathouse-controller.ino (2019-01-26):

#include "Config.h"

//--------------------------------------

#include <Arduino.h>

#include <ESP8266WiFi.h>

#include <ESP8266HTTPClient.h>

#include <EEPROM.h>
#include <OneWire.h>

#include "WiFiUtil.h"
#include "WiFiMain.h"
#include "EEJsonConfig.h"
#include "SerialOS.h"
#include "Util.h"
#include "TempDev.h"
#include "WeightDev.h"
#include "Stats.h"
#include "Engine.h"

void setupPorts()
{
  pinMode(A0, INPUT);

  pinMode(MOSFET_P1, OUTPUT);
  digitalWrite(MOSFET_P1, LOW);

  pinMode(MOSFET_P2, OUTPUT);
  digitalWrite(MOSFET_P2, LOW);

  pinMode(MOSFET_P3, OUTPUT);
  digitalWrite(MOSFET_P3, LOW);

  pinMode(MOSFET_P4, OUTPUT);
  digitalWrite(MOSFET_P4, LOW);

  pinMode(LED_PIN, OUTPUT);
  digitalWrite(LED_PIN, LOW);

  pinMode(FAN_PIN, OUTPUT);
  digitalWrite(FAN_PIN, LOW);
}

//=============================================================
// SETUP
//=============================================================

void setup()
{
  Serial.begin(SERIAL_SPEED);
  //  Serial.swap(); // use D8(TX) - D7(RX)

  Serial.printf("Initial delay...\n");
  {
    //long m = millis();
    //while (timeDiff(m, millis()) < 5000) ;
    delay(5000);
  }

  Serial.printf("STARTUP\n");

  initEEStaticConfig();

  eeJsonConfig.LoadFromEEProm();

  statsInit();

  setupPorts();

  // set led before wifi
  pinMode(LED_BUILTIN, OUTPUT);

  reconnectWifi();

  setupTemperatureDevices();

  Serial.printf("SETUP DONE\n");
}

//=============================================================
// LOOP
//=============================================================

bool systemIsOn = false;

void loop()
{
  {
    freeram = freeMemorySum();
    freeram_min = min(freeram, freeram_min);
  }

  if (manageWifi())
    return;

  if (!serialOsActivated)
    statsUpdate();

  if (!serialOsActivated)
    manageTemp();

  if (!serialOsActivated)
    engineProcess();

  if (Serial.available())
  {
    builtinLedOff();

    auto c = (char)Serial.read();
    if ((int)c != 255)
    {
      if (c == '?' && serialInput.length() == 0)
      {
        printSyntaxHelp();
        serialOsActivated = true;
      }
      else if (c == '\r')
        processSerialCmd();
      else if (c == 8) // backspace
        serialInput.remove(serialInput.length() - 1);
      else
        serialInput.concat(c);
    }

    builtinLedOn();
  }
}

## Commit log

2018-10-07 vscode settings ( see also https://github.com/devel0/knowledge/blob/7adb588b7419af2d8cc202991c49e793ff51a962/arduino/vscode-arduino.md ) ; temperature sensor
2018-10-07 fixed header cleanup ; added timediff util
    [cathouse-controller.ino]
2018-10-10 temperature, led switch ; interactive page
2018-10-11 fixed serial begin macro
    [cathouse-controller.ino]
2018-10-11 fixed wifi init missed call
    [cathouse-controller.ino]
2018-10-13 temperature device by its own 8 byte address
2018-11-28 testing version
    [case-power-supply.fcstd, elbox.scad, elbox.stl]
2018-11-29 beta version
    [esp8266-labels.dxf, project.dxf, tagli materiale.dxf]
2018-12-01 walkthrough analysis
    [esp8266-labels.dxf, project.dxf]
2018-12-01 added ports, led, fan indicators ; added temperature trend ; fixed gen-h for js newlines
    [TempDev.cpp, WiFiUtil.cpp, app.js.h]
2018-12-07 firmware config with analysis variables and reset to factory defaults
    [esp8266-labels.dxf, project.dxf]
2018-12-07 fixed eeprom config load/save
    [cathouse-controller.ino]
2018-12-07 save config through POST (multi frame)
2018-12-17 rework using eeprom json config
    [Config.h, EEJsonConfig.cpp, EEStaticConfig.cpp]
2018-12-17 fixed eejsonconfig save temp id ; enabled temp and stat processes
    [Config.h, EEJsonConfig.cpp, SerialOS.cpp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]
2018-12-20 fix enable cors not considered due to missing include config.h
    [WiFiUtil.cpp]
2018-12-21 rearrangement of html for responsive device ; added adc weight graph
2018-12-21 fixed cat enter/exit detect
    [WeightDev.cpp]
2018-12-22 adc weight last sample cnt configurable ( increased from 10 to 20 )
2018-12-22 verbose info about parsing of temp sensor string from webapi json saveconfig
2018-12-22 log temp device id if tbottom not available
2018-12-22 manual mode p1,p2,p3,p4,led,fan control
2018-12-22 fixed temp assigned identification
    [TempDev.cpp]
2018-12-23 fix poweroff cycle for fanless mode
    [Engine.cpp]
2018-12-30 ensure diabled ports regardless current cycle if cat isn't in there
2019-01-03 verbose info engine millis(), html prev / current cycle
2019-01-04 allow toggle of led port even in manual mode
2019-01-04 biarray catin,p1,p2,p3,p4,fan,disabled,cooldown
2019-01-04 added build to arduino.json to speed up compilation
2019-01-05 step up 3d box
    [step-up-box.stl]
2019-01-05 ambient vs extern temperature graph
2019-01-06 ver 0.83
    [auto-cycle.dxf]
2019-01-06 disable fan when switching from fullpower to standby
2019-01-06 fix tbottom trend eval (standby mode)
    [Config.h, Engine.cpp]
2019-01-06 default tbottom gte 35C fan on
2019-01-24 60 samples ( about 2 min ) for adc weight eval
2019-01-24 threshold 1C for fan disable after it was enabled
2019-01-24 reduced temp sensor resolution
2019-01-25 fixed debug engine info about adcWeightArrayOffLastEvent and fixed cat exit caused by adc weight avg decrease (noise, etc) when toggling cat is in there manually for a preheat;
    [WeightDev.cpp]
2019-01-25 20 samples enough
2019-01-25 fixed cat exit caused by adc weight avg decrease (noise, etc) when toggling cat is in there manually for a preheat
    [WiFiMain.cpp]
2019-01-25 fixed unset manual when enable manual mode and disable after through config manualMode false value
    [Engine.cpp]
2019-01-26 adc weight compensation fixed ; cat in there msg fixed
    [Config.h, WeightDev.cpp]
2019-01-26 temp read failure reporting ; avoid to store fail temp -127 ( use previous if any )
    [TempDev.cpp, WiFiMain.cpp, app.js.h]
2019-01-26 highlight temp failure count if any
    [app.js.h]
2019-01-27 weight sensor last sample cnt info
2019-02-01 v0.86 ( pressure sensor )
2019-02-01 fix twood gte fan on enable
    [Engine.cpp]
2019-02-01 fix cat in there set to false once
    [WeightDev.cpp]
2019-02-01 fix missing pfan var
    [Engine.cpp]
2019-02-02 replaced trend with temperature follower
    [Engine.cpp, app.js.h]
2019-02-02 adj print format
2019-02-02 avoid set cooldown if current cycle none
    [Engine.cpp]
2019-02-02 fixed set ports quantity call
    [Engine.cpp]
2019-02-02 fixed engine active mode
    [Engine.cpp]
2019-02-02 fix catInThereOverriden not disabled when cat enters
    [WeightDev.cpp]
2019-02-05 adc pressure value info
2019-02-09 load cell 5kg
    [bom.xlsx, load-cell-5kg-contact-pad.dxf, load-cell-5kg-contact-pad.fcstd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]
